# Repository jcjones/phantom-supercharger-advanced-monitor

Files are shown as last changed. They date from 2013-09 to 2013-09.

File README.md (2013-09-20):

Phantom Full Throttle Supercharger - Advanced Display
=====================================================

Datalogging, and more visualizations of the electric-powered full-throttle supercharger from [Phantom Superchargers](http://www.phantomsuperchargers.com/)

Bill of Materials
------------------------
* Arduino Uno [@Adafruit](http://www.adafruit.com/products/50)
* Adafruit Datalogging Shield [@Adafruit](http://www.adafruit.com/products/1141)
* Radioshack mini DPDT relay [@RadioShack](http://www.radioshack.com/product/index.jsp?productId=2062483)
* Monochrome 0.96" 128x64 OLED graphic display [@Adafruit](http://www.adafruit.com/product/326)
* 1x PN2222 NPN Transistor [@Adafruit](http://www.adafruit.com/products/756)
* 1 1N4001 diode [@Adafruit](http://www.adafruit.com/products/755)
* 2x DS 18B20 Digital Temperature sensors [@Adafruit](http://www.adafruit.com/products/374)
* 1x 1 M Ohm resistor
* 1x 200 k Ohm resistor
* 3x 1k ohm resistors
* 1x 440 ohm resistor
* 1x SD card for logging
* Wire, various colors
* Perfboard / Protoboard
* 3/4 inch and 1/8 inch heatshrink, for temperature probes
* High-temperature tape (For temperature probes)

Circuit Design
------------------------
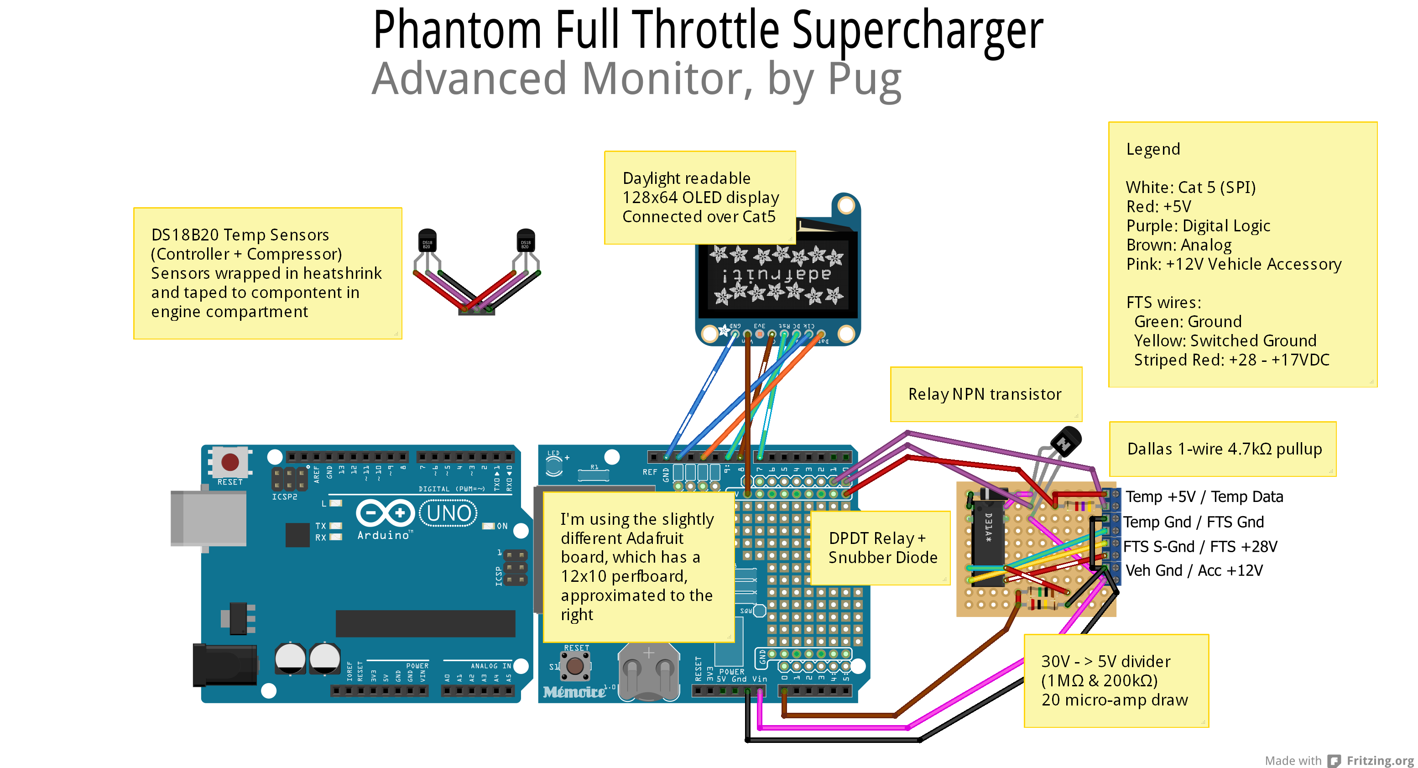
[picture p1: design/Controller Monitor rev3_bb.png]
Breadboard Design

Diagram exports and original files are in the [./design/]() folder. 

### Errata
There is also an [errata list](./design/Errata.md) of things not currently included in the diagrams.

Compiling
------------------------
Use the Arduino IDE; you must install the dependencies as libraries within dependencies/ . That includes installing u8glib, which must be downloaded and installed. See [./dependencies/README.md]()

To download the submodules:
```
 git submodule init
 git submodule update
```

See [./dependencies/README.md]() for instructions on loading them into the Arduino IDE; in particular the U8glib library needs special care.

Usage
------------------------
You must ensure the Real-time Clock is set before logging can function; load, compile, install and run the *ds1138* sketch example once to set the clock. Then you should re-compile and load the Monitor software immediately, as the ds1138 sketch will set the RTC clock to its' compile time each time it starts.

Next Steps
------------------------
After proving the circuit in real-world testing, the next revision is planned to be rendered to PCB form for added compactness. Given the lack of Fritzing-based fabrication facilities, rev 5 of the circuit design will be based on EagleCAD.

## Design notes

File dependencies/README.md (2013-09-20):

Dependencies
============

Each dependency must be loaded into the Arduino IDE by selecting Libraries -> Add Library

* RTClib as a git submodule at commit 573581794b73dc70bccc659df9d54a9f599f4260
* u8glib v1.13 (Arduino Environment) as a forked sudmobule at commit 32689c23d41eebf70e3341bc5e18ea4d4fa82d86 , or downloaded from [https://code.google.com/p/u8glib/downloads/detail?name=u8glib_arduino_v1.13.zip]
* Adafruit SD library as a git submodule at commit 3216c04075860edece362818c9c413e9c061a186
* OneWire as a git submodule at commit 85d1aae63ea4919c64151e03f7e24c2efbc40198

Notes on the U8glib
-------------------
If you choose to use the git submodule, you will need to produce an "arduino" release; do that by running 
> dependencies/u8glib/tools/release/arduino/create_release.sh
and then importing the resulting U8glib folder at dependencies/u8glib/tools/release/arduino/libaries into the IDE.

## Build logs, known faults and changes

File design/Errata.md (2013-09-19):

Errata, rev3:
=============

* NPN Transistor must sink to ground; it is on the wrong side
* NPN Transistor must have a 440 Ohm resistor in series on its Base pin to reduce current
* NPN Transistor connects to digital 4, not 0
* Dallas 1-wire connects to digital 3, not 1
* Button added to digital 2
* Button uses striped orange Cat5 wire and the 5V brown cat5 wire
* Button has 1k pull-down resistor to ground
* Digital 0 and 1 are USB/serial and should be NC
* Diode is pictured backward
* Radio Shack relay is longer than pictured, causing it not to fit
* Terminals pictured were unavailable; real terminals are 3 pins wide with only 2 pins terminating

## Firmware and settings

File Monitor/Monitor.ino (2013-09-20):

#include <OneWire.h>
#include "Globals.h"
#include "U8glib.h"


/* Analog */
#define VOLT_ONE A3
#define AREF_VOLTAGE 5.0

/* Digital */
#define BUTTON 2
#define ONEWIRE 3
#define RELAY 4

/* Hardware SPI */
#define SD_CLK SCK
#define SD_MISO MISO
#define SD_MOSI MOSI
#define SD_CS SS
     
/* Software SPI */
#define OLED_CLK SCK
#define OLED_MOSI MOSI
#define OLED_DC 9
#define OLED_CS 8
#define OLED_RESET 7

OneWire  oneWire(ONEWIRE);
/* OneWire scratchpad */
byte scratchPad[9];

/* Addresses for the 1-wire temperature probes */
byte controllerThermometer[] = { 0x28, 0xF1, 0x14, 0xB3, 0x04, 0x00, 0x00, 0xBF };
byte motorThermometer[] = { 0x28, 0x0D, 0xDE, 0xB2, 0x04, 0x00, 0x00, 0xA0 };

/* Used to space out periodic tasks */
long lastLogUpdate = 0;
long lastTempUpdate = 0;
long stateEndTimeMs = 0;

/*
from pins_arduino.h:
 const static uint8_t SS = 10;
 const static uint8_t MOSI = 11;
 const static uint8_t MISO = 12;
 const static uint8_t SCK  = 13;
 */
 
/*
Conversion Table
------------------------------------
SPI | Cat5 wire colors | Digital Pin
------------------------------------
5V  | Brown            | -
Gnd | S-Blue           | -
Data| Orange           | 11
Clk | Blue             | 13
DC  | Green            | 9
Rest| S-Green          | 7
CS  | S-Brown          | 8
Butt| S-Orange         | 2 (button)
*/

/* Screen */
U8GLIB_SSD1306_128X64 u8g(OLED_CLK, OLED_MOSI, OLED_CS, OLED_DC, OLED_RESET); // HW SPI Com: CS = 10, A0 = 9 (Hardware Pins are  SCK = 13 and MOSI = 11)

float controllerTempC;
float motorTempC;
int sensorVoltOneI;

int lastButtonState = LOW;


// Used by the Fatal state
char onscreenNoticeMessage[33];

#define STATE_SPLASH 0
#define STATE_COUNTDOWN 1
#define STATE_NOTICE 8
#define STATE_FATAL 9
#define STATE_NORMAL 2
#define STATE_DISABLED 3
int displayState;


/* Set the temperature probes to high resolution */
void configureTempResolution() {
  scratchPad[CONFIGURATION] = TEMP_12_BIT;

  oneWire.reset();
  oneWire.skip(); 
  oneWire.write(WRITESCRATCH);
  
  oneWire.write(scratchPad[HIGH_ALARM_TEMP]); // high alarm temp
  oneWire.write(scratchPad[LOW_ALARM_TEMP]); // low alarm temp
  oneWire.write(scratchPad[CONFIGURATION]); // configuration
  
  oneWire.reset();
  oneWire.skip();
  oneWire.write(COPYSCRATCH, NOT_PARASITE);
} 

/* Tell the probes to sample the temperature and store it in their EEPROM */
void requestTemps() {
  
  oneWire.reset();
  oneWire.skip();
  oneWire.write(STARTCONVO, NOT_PARASITE);
}


/* Read the EEPROM of one of the probes, identified by the address */
float readTemp(byte *addr) {
  byte crc;
  byte i;
  
  oneWire.reset();
  oneWire.select(addr);
  oneWire.write(READSCRATCH);
  // read the response

  // byte 0: temperature LSB
  scratchPad[TEMP_LSB] = oneWire.read();

  // byte 1: temperature MSB
  scratchPad[TEMP_MSB] = oneWire.read();

  // byte 2: high alarm temp
  scratchPad[HIGH_ALARM_TEMP] = oneWire.read();

  // byte 3: low alarm temp
  scratchPad[LOW_ALARM_TEMP] = oneWire.read();

  // byte 4:
  // DS18S20: store for crc
  // DS18B20 & DS1822: configuration register
  scratchPad[CONFIGURATION] = oneWire.read();

  // byte 5:
  // internal use & crc
  scratchPad[INTERNAL_BYTE] = oneWire.read();

  // byte 6:
  // DS18S20: COUNT_REMAIN
  // DS18B20 & DS1822: store for crc
  scratchPad[COUNT_REMAIN] = oneWire.read();

  // byte 7:
  // DS18S20: COUNT_PER_C
  // DS18B20 & DS1822: store for crc
  scratchPad[COUNT_PER_C] = oneWire.read();

  // byte 8:
  // SCTRACHPAD_CRC
  scratchPad[SCRATCHPAD_CRC] = oneWire.read();

  oneWire.reset();
  
  crc = OneWire::crc8(scratchPad, 8);
  if (crc != scratchPad[8]) {
    return 0.0;
  }
  
  int16_t raw = (scratchPad[TEMP_MSB] << 8) | scratchPad[TEMP_LSB];

  byte cfg = (scratchPad[4] & 0x60);
  // at lower res, the low bits are undefined, so let's zero them
  if (cfg == 0x00) raw = raw & ~7;  // 9 bit resolution, 93.75 ms
  else if (cfg == 0x20) raw = raw & ~3; // 10 bit res, 187.5 ms
  else if (cfg == 0x40) raw = raw & ~1; // 11 bit res, 375 ms
  
  return (float) raw / 16.0;
}

/* Read all temperature probes and fill in the global variables */
void readTempSensors()
{
  controllerTempC = readTemp(controllerThermometer);
  motorTempC = readTemp(motorThermometer);
}

/* Read all the voltage sensors and fill in the global variables */
void readVoltSensors()
{  
  analogRead(VOLT_ONE); // Discard the first read
  sensorVoltOneI = analogRead(VOLT_ONE);
  
  // fake it
//  sensorVoltOneI = constrain((millis()/10)%1023, 440, 1023); // fake fake TODO
//  sensorVoltOneI = (int)(292.0*sin(millis()/5000.0)+732.0);
 
//  sensorVoltOne = sensorVoltOneI * (29.73 / 1024.0);

//  Serial.print(F("Read Val: "));
//  Serial.print(sensorVoltOneI);
//  Serial.print(F("  Conv: "));
//  Serial.print(sensorVoltOne);
  
  sensorVoltOneI = map(sensorVoltOneI, 0, 1024, 0, 299);
 
//  Serial.print(F("  Int: "));
//  Serial.println(sensorVoltOneI);
  
  addBarGraphDataPoint(sensorVoltOneI);
}

/* Only trigger on a state change to HIGH */
boolean readButtonState() {
  boolean result = false;
  int buttonState = digitalRead(BUTTON);
  
  if (HIGH == buttonState && LOW == lastButtonState) {
    result = true;
  }
  
  lastButtonState = buttonState;
  
  return result;
}

/* Show an error and stop */
void showFatal(const char* buf){
  onscreenNoticeMessage[0] = '\0';
  strncpy(onscreenNoticeMessage, buf, sizeof(onscreenNoticeMessage));
  Serial.print(F("FATAL ERROR:"));
  Serial.println(onscreenNoticeMessage);
  changeState(STATE_FATAL);
}

/* Show a notice and continue */
void showNotice(const char* buf){
  onscreenNoticeMessage[0] = '\0';
  strncpy(onscreenNoticeMessage, buf, sizeof(onscreenNoticeMessage));
  Serial.println(onscreenNoticeMessage);
  changeState(STATE_NOTICE);
}


/* Do state updates for Normal and Disabled states */
void loopNormalAndDisabled() {
  readVoltSensors();
    
  long time = millis();
  
  if (time - TEMP_READ_INTERVAL_MS > lastTempUpdate) {
    lastTempUpdate = time;
    /* Read the most recent values */
    readTempSensors();
    /* Let them process in the background */
    requestTemps();
  }
  
  if (time - DISK_WRITE_INTERVAL_MS > lastLogUpdate) {
    lastLogUpdate = time;
    
    /* Write to disk */
    logData(sensorVoltOneI, motorTempC, controllerTempC);

  }

  // Update the boost info
  updateBoostDuration();  
}


/* Operate the OLED display */
void draw() {
  switch (displayState) {
    case STATE_FATAL:
      u8g.setColorIndex(1);
      u8g.setFont(u8g_font_6x10r);
      u8g.drawFrame(0, 0, DISPLAY_WIDTH, 34);
      u8g.drawStr( 28, 12, F("FATAL ERROR:"));
      u8g.drawStr( 6, 24, onscreenNoticeMessage);
      break;
    case STATE_NOTICE:
      u8g.setColorIndex(1);
      u8g.setFont(u8g_font_6x10r);
      u8g.drawFrame(0, 0, DISPLAY_WIDTH, DISPLAY_HEIGHT);
      u8g.drawStr( 41, 12, F("Notice:"));
      u8g.drawStr( 6, 24, onscreenNoticeMessage);
      u8g.drawStr( 26, 61, F("Press button."));      
      break;
    case STATE_SPLASH:
      u8g.setColorIndex(1);
      u8g.setFont(u8g_font_6x10r);
      u8g.drawStr( 27, 22, F("   PHANTOM   "));
      u8g.drawStr( 27, 34, F("FULL-THROTTLE"));
      u8g.drawStr( 29, 46,  F("SUPERCHARGER"));
      break;
    case STATE_COUNTDOWN:
      u8g.setFont(u8g_font_6x10r);
      u8g.drawStr( 26, 22, F("Starting in:"));
      
      u8g.setFont(u8g_font_helvB24n);
      u8g.setPrintPos(40, 63);      
      {
        long timeLeftMillis = stateEndTimeMs - millis();
        float timeLeftSeconds = 0.0;
        /* Print 0.0 if the remaining millis is not positive */
        if (timeLeftMillis > 0) {
          timeLeftSeconds = (timeLeftMillis) / 1000.0;        
        }
        u8g.print(timeLeftSeconds, 1);        
      }
      break;
    case STATE_NORMAL:
      u8g.setColorIndex(1);
      u8g.setFont(u8g_font_6x10r);
      u8g.setPrintPos(2, 10);
      u8g.print(F("MOT "));
      u8g.print(motorTempC, 1);
      u8g.print(F("C   CPU "));
      u8g.print(controllerTempC, 1);
      u8g.print(F("C"));
      
    
      if (isBoosting()) {
        u8g.setPrintPos(40, 20);
        u8g.print(F("Boosting"));
      } else { 
        u8g.setPrintPos(10, 20);     
        u8g.print(F("Last Boost: "));
        u8g.print(getLastBoostDurationMillis()/1000.0, 2);
        u8g.print(F(" s"));
      }
      
      for(int i=0; i<BARGRAPH_DATA_SZ; i++) {
        int h = getBarGraphDataPointInPast(i);
        int x = i*2;
        int yStart = DISPLAY_HEIGHT - h;
        u8g.drawVLine(DISPLAY_WIDTH-x, yStart, h);
        u8g.drawVLine(DISPLAY_WIDTH-x+1, yStart, h);        
      }
      

      u8g.setColorIndex(0);
      u8g.drawRBox(30, 36, 72, 28, 2);

      u8g.setColorIndex(1);
      u8g.drawRFrame(30, 36, 72, 28, 2);      

      u8g.setFont(u8g_font_helvB24n);
      u8g.setPrintPos(34, 63);
      u8g.print(sensorVoltOneI/10);
      u8g.print(".");
      u8g.print(sensorVoltOneI - (sensorVoltOneI/10*10)); 
      
      break;   
case STATE_DISABLED:
      u8g.setColorIndex(1);
      u8g.setFont(u8g_font_6x10r);
      u8g.setPrintPos(2, 10);
      u8g.print(F("MOT "));
      u8g.print(motorTempC, 1);
      u8g.print(F("C   CPU "));
      u8g.print(controllerTempC, 1);
      u8g.print(F("C"));
     
      u8g.setColorIndex(1);      
      u8g.drawStr( 20, 61, F("Press to Enable"));      
      break;         
  }
}


void setup()   {       
  Serial.begin(9600);
  
  u8g.setHardwareBackup(u8g_backup_avr_spi);
  
  pinMode(SD_CS, OUTPUT);
  pinMode(OLED_CS, OUTPUT);
  pinMode(RELAY, OUTPUT);
  pinMode(BUTTON, INPUT);
   
  changeState(STATE_SPLASH);

  // Setup bar graph
  setupBarGraph();
}


/* State change function */
void changeState(int newState) {
//  Serial.print(F("S_OLD: "));
//  Serial.print(displayState);  
//  Serial.print(F("   S_NEW: "));
//  Serial.println(newState);  
  displayState = newState;
  
  switch (displayState) {
    case STATE_NORMAL:
      Serial.println(F("Relay enabled"));
      digitalWrite(RELAY, HIGH);   
      break;    
    case STATE_DISABLED:
      Serial.println(F("Relay disabled"));
      digitalWrite(RELAY, LOW);    
      break;
    case STATE_COUNTDOWN:
      stateEndTimeMs = millis() + COUNTDOWN_TIME_MS;
      break;
  }
}


void loop() {
  
  /* Draw */
  u8g.firstPage();  
  do {
    draw();
  } while( u8g.nextPage() );

  /* Load button state */
  boolean buttonPressed = readButtonState();
  
 
  /* State updates */
  switch(displayState){
    case STATE_SPLASH:    
      /* Initialize the data logger */
      DataLogging_Begin(SD_CS, SD_MOSI, SD_MISO, SD_CLK);
      
      /* Set up the temperature probes */
      configureTempResolution();
      
      /* Request the first temperatures */
      requestTemps();
      
      /* Remain in splash for 2 seconds */
      delay(2000);
      
      /* Move to Countdown. */
      changeState(STATE_COUNTDOWN);     
      
      break;
    case STATE_FATAL:
      while(1) {
        // Hold here forever
      }
      break;
    case STATE_NOTICE:
      if (buttonPressed) {
        /* Return to Normal. */
        changeState(STATE_NORMAL);
      }
      
      break;
    case STATE_COUNTDOWN:
      if (stateEndTimeMs < millis() || buttonPressed) {
        /* Return to Normal. */
        changeState(STATE_NORMAL);
      }
            
      break;
    case STATE_NORMAL:
      if (buttonPressed) {
        changeState(STATE_DISABLED);        
      }
      
      loopNormalAndDisabled();
      break;
    case STATE_DISABLED:
      if (buttonPressed) {
        changeState(STATE_NORMAL);        
      }
    
      loopNormalAndDisabled();
      break;
   }
  
  delay(CYCLE_DELAY);
}

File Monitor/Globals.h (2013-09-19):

#ifndef Globals_h
#define Globals_h

#include "Arduino.h"

#define DISPLAY_WIDTH 128
#define DISPLAY_HEIGHT 64

#define GRAPH_HEIGHT 40
#define GRAPH_WIDTH BARGRAPH_DATA_SZ

#define BARGRAPH_DATA_SZ 64

#define CYCLE_DELAY 50
#define DISK_WRITE_INTERVAL_MS 1000
#define TEMP_READ_INTERVAL_MS 500
#define COUNTDOWN_TIME_MS 10000

#define ONEWIRE_POWERED_POLLTIME_MS 100

// OneWire Commands
#define STARTCONVO      0x44  // Tells device to take a temperature reading and put it on the scratchpad
#define READSCRATCH     0xBE  // Read EEPROM
#define WRITESCRATCH    0x4E  // Write to EEPROM
#define COPYSCRATCH     0x48  // Copy EEPROM

// OneWire Configurations
#define TEMP_12_BIT 0x7F // 12 bit

// OneWire Scratchpad locations
#define TEMP_LSB        0
#define TEMP_MSB        1
#define HIGH_ALARM_TEMP 2
#define LOW_ALARM_TEMP  3
#define CONFIGURATION   4
#define INTERNAL_BYTE   5
#define COUNT_REMAIN    6
#define COUNT_PER_C     7
#define SCRATCHPAD_CRC  8

#define NOT_PARASITE  0

#endif // Globals_h

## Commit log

2013-08-21 Change to the sin() function for voltage fakery
2013-09-07 Switch to digital sensors
2013-09-08 Added button to state machine
2013-09-19 Prepare for release
    [Controller Monitor rev3.fzz]
